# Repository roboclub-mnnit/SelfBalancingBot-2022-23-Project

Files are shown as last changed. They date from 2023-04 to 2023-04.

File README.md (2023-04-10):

# Self Balancing bot

## Robot Image



## Aim 

To balance a robot on two wheels at its normal position and control its movement through an Android app.

# Introduction

The aim of this project is to make an automated vehicle that balances itself without any outside help or support. This project is a rather complex one as it involves using PID Control and involuted programming. Self-balancing robots are unique among all others, just because of their ability to balance on a given fixed position. Even if the robot is displaced from its position, it is programmed so that it again recovers its position.

## Technology used

**On Robot:** Bluetooth, PID, TIMER Interrupt, Kalman Filter, Communication protocol (serial and I2C).

## Components

**MPU6050:** MPU6050 is a three-axis accelerometer and three-axis gyroscope Micro Electro-mechanical system (MEMS). It aids in the measurement of velocity, orientation, acceleration, displacement, and other motion-related features.

**Arduino Uno:** Arduino UNO is a low-cost, flexible, and easy-to-use programmable open-source microcontroller board that can be integrated into a variety of electronic projects. This board can be interfaced with other Arduino boards, Arduino shields, and Raspberry Pi boards and can control relays, LEDs, servos, and motors as an output.

**Drv8825 Motor driver:** The Drv8825 is a complete micro-stepping motor driver with a built-in translator for easy operation. It is designed to operate bipolar stepper motors in full-, half-, quarter-, eighth-, and sixteenth-step modes, with an output drive capacity of up to 45 V and ±2.2 A.

**Stepper Motor:** Stepper motors are a type of DC synchronous motor. Whereas the rotation of an induction motor is largely uncontrollable, the rotation of a stepper motor can be controlled with a remarkable degree of precision. Stepper motors can produce full, instantaneous torque - even from a standstill.

**ESP32:** ESP32 can perform as a complete standalone system or as a slave device to a host MCU, reducing communication stack overhead on the main application processor. ESP32 can interface with other systems to provide Wi-Fi and Bluetooth functionality through its SPI / SDIO or I2C / UART interfaces.

**Li-polymer battery:**  A lithium-polymer battery (LiPo) is a rechargeable battery that, in the case of true LiPo, uses solid polymer for the electrolyte and lithium for one of the electrodes. Commercially available LiPo is a hybrid: gel polymer or liquid electrolyte in a pouch format, more accurately termed a lithium-ion polymer battery.

**Jumper wire  :** Jumper wires typically come in three versions: male-to-male, male-to-female and female-to-female. The difference between each is in the endpoint of the wire. Male ends have a pin protruding and can plug into things, while female ends do not and are used to plug things into.

## Role of each software component-

**MPU6050 Data:** Initially MPU-6050 will measure the angle difference between the current position of the bot and its normal position. Now, this data is transferred to PID.

**PID Tuning:** PID will take input from MPU-6050 and accordingly calculate the PID value and give variable signals to both motors using interrupt service routine to bring the bot to its normal position and balance it.

**Bluetooth Communication:** Once the bot is balanced then we will send different commands ( forward, backward, turn left, turn right, and stop ) to the bot using Bluetooth communication to move the bot in different directions.

**ISR Command:** After receiving a command from Bluetooth, ISR will give different impulses to motors to move the bot according to the given command.

## Working of the bot

**1.** Turning the robot on.

**2.** The servo motor position is set to a minimum position to keep the robot in a standing position.

**3.** Receiving the data from Bluetooth.

**4.** Data is collected from the mpu-6050 and robot angle is calculated.

**5.** Data from MPU-6050 is filtered to remove the noise and make the data stable

**6.** Feeding the data in the PID controller and error is calculated by comparing it with the bot’s current angle and the balance point is delivered as output from the PID controller which will be in a linear data form.

**7.** Converting the linear PID balance point into a logarithmic balance point for running the stepper motor at variable speed.

**8.** Controlling the left and right motor separately.

**9.** **a** -->For controlling the left and right turn we changed the balance point of PID  for both motors separately.

**b** -->For moving forward and backward we have changed the target angle where the robot has to balance.
ex.--  Forward→increased target angle 
       Backward→decreased target angle

**10.** Starting the loop again from 3rd point.

## Features

- The robot balances on two wheels.
- We can move the robot left, right, forward, and backward.
- Option to set the PID constants from the onboard knob as well as wirelessly from the Android application.
- The robot stands on its own with a servo motor for calibration when powered on.
- We can reset the robot wirelessly in case it falls on the ground.
- Used PORT control of Arduino for making the pin high and low as it is 60 times faster than the digitalWrite function of Arduino. 

## Circuit diagram

Self balancing circuit

## App interface

bot

## App link

[Self balancing bot app.zip](https://github.com/sudhanshur555/SelfBalancingBot-2022-23-Project/files/11194098/Self.balancing.bot.app.zip)

## Source Code

[https://github.com/roboclub-mnnit/SelfBalancingBot-2022-23-Project](https://github.com/roboclub-mnnit/SelfBalancingBot-2022-23-Project)

## Video link

- https://youtu.be/lqwXdpySzbQ

## Real-life applications

- Self-balancing algorithms can be used in rocket propulsion systems.
- Can be used in warehouses for moving goods.
- It can be implemented on Segway.
- It can be used for surveillance in any terrain.

## Problem faced

**1.** MPU-6050 data has a lot of noise so we have a Kalman filter to smooth the data.

**2.** The setting of the PID value was frustrating when setting in code each time and checking the robot whether it is balanced or not. so we made three knobs to adjust the PID constant onboard without changing it in code and we also added this feature in the app so that the PID constant can also be set wirelessly.

**3.** Bluetooth connection gets lost regularly afterward we figured out that the input voltage was under 5v. So we powered the ESP32 directly with a battery with 11v.

**4.** When the potentiometer(for setting the PID constants) was powered with a 7805 voltage regulator(for 5v output) the robot oscillates as the servos were also connected to the 7805 and it drew a lot of power which made it undervolt(less than 5v)  and the value of constants gets changed when mapped in Arduino code. So we powered it directly with 5v of Arduino to get stable 5v.

**5.** Earlier we used TIMER1 interrupt (ISR) but later realized that it was causing the problem as servo library we have used also use TIMER1 to make PWM signal and delay function in Arduino uses TIMER0 for delay function so we have used the this Arduino ISR i.e TIMER2 for creating interrupt for making Stepper motor impulse.

**7.** Stepper motor was not turning at a very high speed so we have chosen an ISR of 200us as full speed for the stepper motor.

**8.** The bot was getting resettled in the setup part of the code in  which we had defined D13 as output and didn't work so we had defined the D13 as output in an “IF statement” in the loop part of the code.

**9.** To prevent the potentiometer and app PID constant from clashing with the original PID constant which we have set in code we have set a range so that we can deactivate the Potentiometer and app PID constant values when not needed and activate it only When the values Kp & Kd exceeds 10 and Ki exceeds 2.

**10.** Used PORT control of Arduino for making the pin high and low as it is 60 times faster than the digitalWrite function of Arduino and we have used it in ISR to make the impulse for driving the Stepper motor.

**11.** Detached the servo by software after running the main loop 200 times to prevent the oscillation of the servo and also prevent it further from drawing power from the battery.

**12.** Converted the linear output of PID value to nonlinear i.e in Logarithmic value to run the stepper motor at different speeds at different angles.

**13.** Controlled left and right Stepper motors separately for controlling the movement of the robot.

**14.** Made an Android app for controlling the movement of robots.

**15.** Separated the data coming from the app via Bluetooth in string form and stored it in different variables.

**16.** The PID error of Ki was getting very large and affected the responsiveness of the robot so we had limited it in range (-200 to 200).

**17.** There was a problem with the app that it was not showing any Bluetooth devices. Later we found that to connect it with Bluetooth it is first necessary to ask the app for accessing the phone’s Bluetooth. So we added the code in the app to ask for permission for accessing the Bluetooth from a user in the MIT app inventor. 

Note-This issue will only be faced in Android 9+ devices

**18.** Microstepping was used for smoother operation of the stepper motor.

**19.** Always disconnect the Rx and Tx pin of the Arduino while uploading the code to Arduino.

## Resources

 - Stepper motor control
   - Theory
     - https://youtu.be/09Mpkjcr0bo
     - https://youtu.be/eyqwLiowZiU
   - Programming
     - https://www.youtube.com/watch?v=7spK_BkMJys
 - Arduino
   - https://youtube.com/playlist?list=PLGs0VKk2DiYw-L-RibttcvK-WBZm8WLEP

- MPU6050
  - https://youtu.be/XCyRXMvVSCw
  - https://www.youtube.com/watch?v=7VW_XVbtu9k
  - https://youtu.be/yhz3bRQLvBY
  - https://youtu.be/Yh6mYF3VdFQ

- Battery
  - https://www.youtube.com/watch?v=Tye3dcBOqtY

- Servo motor
  - https://youtu.be/kUHmYKWwuWs

- HC-05 Bluetooth module
  - https://www.youtube.com/watch?v=yyjAAbxr0gM

- PID Controller
  - https://youtu.be/crw0Hcc67RY
  - https://youtu.be/t7ImNDOQIzM
  
- Communication 
  - https://youtu.be/IyGwvGzrqp8
  - https://youtu.be/fwGdmU2wi9s

- Filter
  - https://youtu.be/5HuN9iL-zxU

- Interrupt
  - https://youtu.be/Uv9UeYUsA8A

## Contributors

 - [Sudhanshu Ranjan](https://github.com/sudhanshur555)

 - [Abhishek Kumar Singh](https://github.com/Abhishekkumarsingh8957)

 - [Vikas]()

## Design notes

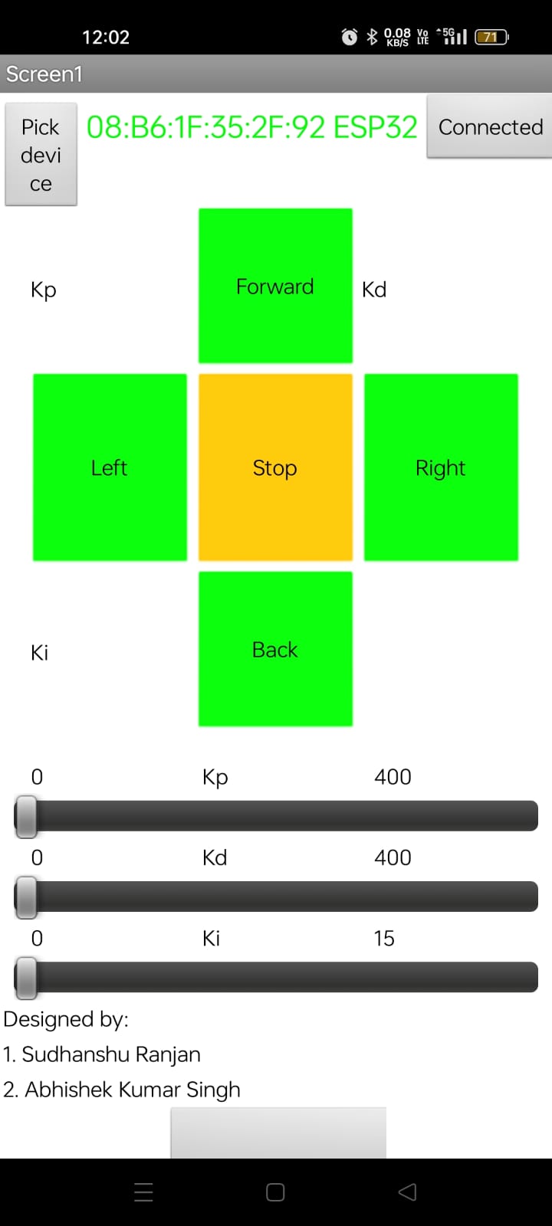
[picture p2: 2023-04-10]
App_interface.jpeg

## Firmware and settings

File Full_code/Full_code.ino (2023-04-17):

#include <Wire.h> //Included Wire library 

// bluetooth variable starts--------------------------------------------------


 int counter =0;
 char c;
 String dataIn;
 int8_t indexOfA,  indexOfB,  indexOfC,  indexOfD, indexOfE,  indexOfF,  indexOfG,  indexOfH ,indexOfI;

 String    data1,  data2,  data3,  data4, data5,  data6,  data7,  data8, data9;

 float newKp_bluetooth=0;
 float newKd_bluetooth=0;
 float newKi_bluetooth=0;

 bool F,B,L,R,S,startagain;

// bluetooth variable ends--------------------------------------------------


// potentiometer variable starts=============================================

float pot1=0;
float pot2=0;
float pot3=0;
float newkp_pot=0;
float newkd_pot=0;
float newki_pot=0;


// potentiometer variable ends=============================================


// servo declaration starts---------------------------------

  #include <Servo.h>
  Servo myservo1;  // create servo1 object to control a servo
  Servo myservo2;  // create servo2 object to control a servo
  unsigned long counter2=0;
// servo declaration ends---------------------------------

//mpu variable starts-------------------------------------

float RateRoll, RatePitch, RateYaw;
float RateCalibrationRoll, RateCalibrationPitch, RateCalibrationYaw;
float pitchTarget;
float pitch_Error;
int RateCalibrationNumber;
float AccX, AccY, AccZ;
float AngleRoll, AnglePitch;

//mpu variable ends--------------------------------------

//kalman filter variable starts--------------------------

float KalmanAngleRoll=0, KalmanUncertaintyAngleRoll=2*2;
float KalmanAnglePitch=0, KalmanUncertaintyAnglePitch=2*2;
float Kalman1DOutput[]={0,0};

//kalman filter variable ends--------------------------

//pid variable starts---------------------------------- 

float Kp=112;
float Kd=316;
float Ki=1.80;

float Kp_old=Kp;
float Kd_old=Kd;
float Ki_old=Ki;

//pid variable ends------------------------------------
float rotating_speed=100;

unsigned long milliOld;
unsigned long milliNew; 
unsigned long dt;


//Declaring global variables for mpu

float rollTarget=-4.70;
float rollActual;
float rollError=0;
float rollErrorOld;
float rollErrorChange;
float rollErrorSlope=0;
float rollErrorArea=0;
float rollBalance=0;
float rollBalance_left=0;
float rollBalance_right=0;


//Defining variable for motor
int New_speed_left;
int New_speed_right;
int speed_motor;
int ISR_counter_left=0;
int ISR_counter_right=0;
int Old_speed_left=0;
int Old_speed_right=0;


void setup() {
Serial.begin(57600);
// servo setup starts---------------------------------
   
   

   myservo1.attach(10);                 // attaches the servo on pin 10 to the servo object
   myservo2.attach(11);                 // attaches the servo on pin 11 to the servo object

   myservo1.write(5);                  // sets the servo position according to the scaled value
   delay(20);
   myservo2.write(20);                  // sets the servo position according to the scaled value
   delay(20);                           // waits for the servo to get there
   delay(2000);

// servo setup ends---------------------------------


  Wire.setClock(400000);  //Setting the clock frequency 400khz for I2C communication
  Wire.begin();
  delay(250);
  Wire.beginTransmission(0x68); 
  Wire.write(0x6B);
  Wire.write(0x00);
  Wire.endTransmission();


//Gyro calibration starts ----------------------------------------------------------------------------

 for (RateCalibrationNumber=0; RateCalibrationNumber<2000; RateCalibrationNumber ++) {  //rinning for loop 2000 times for calibration purpose
    gyro_signals();
    RateCalibrationRoll+=RateRoll;
    RateCalibrationPitch+=RatePitch;
    RateCalibrationYaw+=RateYaw;
    delay(1);
  }
  RateCalibrationRoll/=2000;
  RateCalibrationPitch/=2000;
  RateCalibrationYaw/=2000;  
//gyro calibration ends---------------------------------------------------------------------------------


angle();  //Called angle function


pinMode(A0, INPUT);             //Setting the A0 as input for using potentiometer as input for setting Kp
pinMode(A1, INPUT);             //Setting the A1 as input for using potentiometer as input for setting Kd
pinMode(A2, INPUT);             //Setting the A2 as input for using potentiometer as input for setting Ki

digitalWrite(5,HIGH);           // Setting direction pin of left stepper high for rotating it clockwise
digitalWrite(6,HIGH);           // Setting direction pin of right stepper high for rotating it clockwise
DDRD =B01101100;                //Setting PORTD of arduino to input and output from D2 to D7 by Direction register


//timer2 starts================================================================


   TCCR2A = 0;                                                               //Make sure that the TCCR2A register is set to zero
   TCCR2B = 0;                                                               //Make sure that the TCCR2A register is set to zero
   TIMSK2 |= (1 << OCIE2A);                                                  //Set the interupt enable bit OCIE2A in the TIMSK2 register
   TCCR2B |= (1 << CS21);                                                    //Set the CS21 bit in the TCCRB register to set the prescaler to 8
   TCCR2B |= (1 << CS20);                                                    //Set the CS21 bit in the TCCRB register to set the prescaler to 8
   OCR2A = 99;                                                               //The compare register is set to 200us
   TCCR2A |= (1 << WGM21);                                                   //Set counter 2 to CTC (clear timer on compare) mode


//timer2 ends==================================================================

  milliNew=micros();                                                         //stored current time in milli new for comparing it later

}

void loop() {
  
  //potentiometer  loop starts----------------------------------------------------
Serial.print("kp= ");
   Serial.print(Kp);
   Serial.print("kd= ");
   Serial.print(Kd);
   Serial.print("ki= ");
   Serial.print(Ki);
   Serial.print("rolltarget= ");
   Serial.println(rollTarget);
   
  pot1=analogRead(A0);            //Storing analog value of potentiometer at A0 in pot1 variable
  pot2=analogRead(A1);            //Storing analog value of potentiometer at A1 in pot2 variable
  pot3=analogRead(A2);            //Storing analog value of potentiometer at A2 in pot3 variable



  newkp_pot=map(pot1,0,1023,0,400);  //mapping the value of pot1 to 0-400 and storing it in variable newkp_pot
  newkd_pot=map(pot2,0,1023,0,400);  //mapping the value of pot2 to 0-400 and storing it in variable newkd_pot
  newki_pot=map(pot3,0,1023,0,1500); //mapping the value of pot3 to 0-1500 and storing it in variable newki_pot

  
  if(newkp_pot>10) Kp=newkp_pot;   //putting the condition that the value of newkp_pot will only stored in Kp when it is greater than 10
  if(newkd_pot>10) Kd=newkd_pot;   //putting the condition that the value of newkd_pot will only stored in Kd when it is greater than 10
  if(newki_pot>200) Ki=newki_pot/100;   //putting the condition that the value of newki_pot will only stored in Ki when it is greater than 200


  //potentiometer loop ends-----------------------------------



  //servo loop starts-----------------------------------

 counter2++;                           //increasing the counter2 by one when the servo code starts
 if(counter2>100)                      //executing the condition only when the main loop has already ran 100 times
 {
 myservo1.write(40);                  // sets the servo position to 40 degree
   
 myservo2.write(45);                  // sets the servo position 45 degree

 
 }

if(counter2>200)                      // it gets activated ehen counter2 get higher than 200 i.e the main loop ran 200 times
{

 myservo1.detach();                   //disconnect the servo1 and stop sending the signal to servo1
  myservo2.detach();                  //disconnect the servo1 and stop sending the signal to servo1
}

//servo loop ends----------------------------------------

//bluetooth loop begins=======================================================================



   while(Serial.available()>0)      //The loop activates when the serial buffer has data greater than 1 of arduino
   {
   c=Serial.read();                 //store the buffer data in string "c"
   if(c=='\n') {break;}             // when line change i.e "\n" is detected in string "c" then get out of while loop
   else        {dataIn+=c;}         
   }
   if(c=='\n')
   {
   Parse_the_Data();                //calling the function to storing the data in different variable from data1 to data 9

   F=data1.toInt();                 //Converting the string stored in data1 to integer and storing it in F for moving forward
   S=data2.toInt();                 //Converting the string stored in data2 to integer and storing it in S for stopping robot
   B=data3.toInt();                 //Converting the string stored in data3 to integer and storing it in B for moving robot backward
   
   R=data4.toInt();                 //Converting the string stored in data4 to integer and storing it in R  for turnibg robot rightward
   L=data5.toInt();                 //Converting the string stored in data5 to integer and storing it in L  for turning robot leftward
   newKp_bluetooth=data6.toFloat(); //Converting the string stored in data6 to integer and storing it in newKp_bluetooth  for setting Kp from app
   newKd_bluetooth=data7.toFloat(); //Converting the string stored in data7 to integer and storing it in newKd_bluetooth  for setting Kp from app
   newKi_bluetooth=data8.toFloat(); //Converting the string stored in data8 to integer and storing it in newKi_bluetooth  for setting Kp from app
   startagain=data9.toInt();        //Converting the string stored in data9 to integer and storing it in startagain for resetting arduino when reset button is pressed in app

   c=0;                             // deleting the data stored in "c" for storing new data from serial buffer memory of arduino
   dataIn="";                       // making dataIn blank
   }
  
   if(newKp_bluetooth>10) Kp=newKp_bluetooth;  //putting the condition that the value of newKp_bluetooth will only stored in Kp when it is greater than 10
   if(newKd_bluetooth>10) Kd=newKd_bluetooth;  //putting the condition that the value of newKd_bluetooth will only stored in Kd when it is greater than 10
   if(newKi_bluetooth>1.1) Ki=newKi_bluetooth;   //putting the condition that the value of newKi_bluetooth will only stored in Ki when it is greater than 2

//bluetooth loop ends==========================================================================




 angle();                          //Calling angle() function
  
 rollActual=KalmanAngleRoll;        //storing the current roll angle in rollActual
 
                                                 
 milliOld=milliNew;                 //storing the old time in milliNew
 milliNew=micros();                //storing the current time in milliNew for comparing it with milliold                                                                                              
 dt=milliNew-milliOld;             //Calculating the time difference bw milliNew and milliOld                                                                                         



  rollErrorOld=rollError;
  rollError=rollTarget-rollActual;                                                //error in roll angle wrt reference angle
  rollErrorChange=rollError-rollErrorOld;                                         //difference bw previous and current error
  rollErrorSlope=rollErrorChange/dt;                                              //Slope of error vs time
  rollErrorArea=rollErrorArea+rollError*dt;                                       //adding the previoud roll area and current area



  if(rollErrorArea > 200)rollErrorArea = 200;                                     //limiting the integral value for quicker response
  else if(rollErrorArea < -200)rollErrorArea = -200;

  rollBalance=Kp*rollError+Kd*rollErrorSlope+Ki*rollErrorArea;                    //Calculating the PID Balance point in rollBalance

   if(rollBalance < 10 && rollBalance > -10)rollBalance = 0;                      //consider the robot balanced when rollBalance is from -10to10 and setting rollBalance to 0.

  if(rollBalance > 400)rollBalance = 400;                                        //limit the PID-controller to the maximum controller output i.e 400
  else if(rollBalance < -400)rollBalance = -400;


  if(AngleRoll > 55 || AngleRoll < -55){                                           //stop the robot if it tilt greater than 55 degree
    rollBalance = 0;                                                             //Set the PID controller output to 0 so the motors stop moving
   } 

   
//for controlling bot via app------------------------------------------------------------------------------
 
rollBalance_left=rollBalance;                                                    // storing the value of rollBalance in rollBalance_left variable separately to control left motor separately.
rollBalance_right=rollBalance;                                                   // storing the value of rollBalance in rollBalance_right variable separately to control right motor separately.
 
 if(R==1 || L==1)                                                             //checking the command through bluetooth i.e. left or right
{
 counter++;
// Serial.print("  counter =" );
//  Serial.print(counter);
  if(R==1){                                                                   //rotating the bot in right direction
//     Serial.print("  Right Triggered " );
    rollBalance_left += rotating_speed;                                       //Increase the left motor speed
    rollBalance_right -= rotating_speed;                                      //Decrease the right motor speed
  }
  if(L==1){                                                                   //rotating the bot in left direction         
//    Serial.print("  Left Triggered " );       
    rollBalance_left -= rotating_speed;                                       //Decrease the left motor speed
    rollBalance_right += rotating_speed;                                      //Increase the right motor speed
  }

  
  
 if(counter>20)                                                               //turning the motor in left or right direction for 20 loops when left or right command is recieved through bluetooth
 {
  counter=0;
    R=0;
    L=0;
    F=0;
    B=0;
 }}
 if(F==1){                                                                   //checking for forward command through bluetooth
   rollTarget+=+0.3;                                                         //increasing the balance point of bot by 0.3 degree to move the bot in forward direction 
   F=0;                                                                      //setting again f=0 to avoid the continuous increment of 0.3 degree in set point in every loop
  }
 if(B==1){                                                                   //checking for backward command through bluetooth
    rollTarget+=-0.3;                                                        //decreasing the balance point of bot by 0.3 degree to move the bot in backward direction 
    B=0;                                                                     //setting again b=0 to avoid the continuous decrement of 0.3 degree in set point in every loop
    }   

 if(S==1){                                                                   //checking for stop command through bluetooth 
    rollTarget=-5.2;                                                         //setting the balance point of bot again to normal position i.e.-5.2 degree 
    R=0;                                                                     
    L=0;                                                                     //setting all other commands to zero to stop the bot and balance it at the current position
    F=0;
    B=0;
  }
  if(startagain==1){                  //resetting the arduino when reset buttomn is pressed in app and startagain becomes 1
 pinMode(12, OUTPUT);                //enable pin 12 as output
digitalWrite(12, HIGH);              // setting the D12 as high for resetting the arduino
  }
 
 
 
 
 
// for controlling bot via app-----------------------------------------------------------------------------------------------
 
 
 
 //Motor pulse calculations

//To compensate for the non-linear behaviour of the stepper motors the folowing calculations are needed to get a linear speed behaviour.
//for right motor---
if(rollBalance_right > 0)rollBalance_right = 404 - (1/(rollBalance_right + 9)) * 5500;           //changing the linar behaviour of rollbalance_right variable into logarithmic behaviour which is required to stepper motor
  else if(rollBalance_right < 0)rollBalance_right = -404 - (1/(rollBalance_right - 9)) * 5500;
  if(rollBalance_right > 0)New_speed_right = 394 - rollBalance_right;                            //Calculating the needed pulse time for the  stepper motor controllers
  else if(rollBalance_right < 0)New_speed_right = -394 - rollBalance_right;
  else New_speed_right = 0;


//for left motor----
  if(rollBalance_left > 0)rollBalance_left = 404 - (1/(rollBalance_left + 9)) * 5500;             //changing the linar behaviour of rollbalance_left variable into logarithmic behaviour which is required to stepper motor
  else if(rollBalance_left < 0)rollBalance_left = -404 - (1/(rollBalance_left - 9)) * 5500;
//Calculating the needed pulse time for the  stepper motor                                        //Calculating the needed pulse time for the  stepper motor controllers
  if(rollBalance_left > 0)New_speed_left = 394 - rollBalance_left;
  else if(rollBalance_left < 0)New_speed_left = -394 - rollBalance_left;
  else New_speed_left = 0;

}

//kalman filter function starts--------------------------------------------------------
//KalmanState is the predicted angle at each state , KalmanUncertainty is the uncertainty in predicted angle at each state 
//KalmanInput is the rotation rate is degree/secound measured by gyroscope , KalmanMeasurement is the angle measured by accelerometer trigonometry
void kalman_1d(float KalmanState, float KalmanUncertainty, float KalmanInput, float KalmanMeasurement) {                 
  KalmanState=KalmanState+0.004*KalmanInput;                                           //predicted angle(KalmanState) is calculated by adding previous predicted angle and angle change between previous state and current state             
  KalmanUncertainty=KalmanUncertainty + 0.004 * 0.004 * 4 * 4;                         //uncertainity in predicted angle(KalmanUncertainty) is calculated by adding uncertainity in previous state and iteration length
  float KalmanGain=KalmanUncertainty * 1/(1*KalmanUncertainty + 3 * 3);                //kalmangain is calulated here by ratio of predicted angle and accelerometer angle
  KalmanState=KalmanState+KalmanGain * (KalmanMeasurement-KalmanState);                //new predicted angle is calculated using kalmangain which is much accurate than previous one
  KalmanUncertainty=(1-KalmanGain) * KalmanUncertainty;                                //calculating uncertainity in new predicted angle using kalaman gain
  Kalman1DOutput[0]=KalmanState;                                                       //storing value of predicted angle(KalmanState) in Kalman1DOutput matrix at 0th index
  Kalman1DOutput[1]=KalmanUncertainty;                                                 //storing value of uncertainity in predicted angle(KalmanUncertainty) in Kalman1DOutput matrix at 1st index
}

//kalman filter function ends-----------------------------------------------------------

//gyro_signal function stats------------------------------------------------------------
//this fuction is used to calculate the angle using accelerometer trigonomentry
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

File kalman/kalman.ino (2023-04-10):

#include <Wire.h>
float RateRoll, RatePitch, RateYaw;
float RateCalibrationRoll, RateCalibrationPitch, RateCalibrationYaw;
float rollTarget,pitchTarget;
float Roll_Error,Pitch_Error;
int RateCalibrationNumber;
float AccX, AccY, AccZ;
float AngleRoll, AnglePitch;
uint32_t LoopTimer;
float KalmanAngleRoll=0, KalmanUncertaintyAngleRoll=2*2;
float KalmanAnglePitch=0, KalmanUncertaintyAnglePitch=2*2;
float Kalman1DOutput[]={0,0};
void kalman_1d(float KalmanState, float KalmanUncertainty, float KalmanInput, float KalmanMeasurement) {
  KalmanState=KalmanState+0.004*KalmanInput;
  KalmanUncertainty=KalmanUncertainty + 0.004 * 0.004 * 4 * 4;
  float KalmanGain=KalmanUncertainty * 1/(1*KalmanUncertainty + 3 * 3);
  KalmanState=KalmanState+KalmanGain * (KalmanMeasurement-KalmanState);
  KalmanUncertainty=(1-KalmanGain) * KalmanUncertainty;
  Kalman1DOutput[0]=KalmanState; 
  Kalman1DOutput[1]=KalmanUncertainty;
}
void gyro_signals(void) {
  Wire.beginTransmission(0x68);
  Wire.write(0x1A);
  Wire.write(0x05);
  Wire.endTransmission();
  Wire.beginTransmission(0x68);
  Wire.write(0x1C);
  Wire.write(0x10);
  Wire.endTransmission();
  Wire.beginTransmission(0x68);
  Wire.write(0x3B);
  Wire.endTransmission(); 
  Wire.requestFrom(0x68,6);
  int16_t AccXLSB = Wire.read() << 8 | Wire.read();
  int16_t AccYLSB = Wire.read() << 8 | Wire.read();
  int16_t AccZLSB = Wire.read() << 8 | Wire.read();
  Wire.beginTransmission(0x68);
  Wire.write(0x1B); 
  Wire.write(0x8);
  Wire.endTransmission();     
  Wire.beginTransmission(0x68);
  Wire.write(0x43);
  Wire.endTransmission();
  Wire.requestFrom(0x68,6);
  int16_t GyroX=Wire.read()<<8 | Wire.read();
  int16_t GyroY=Wire.read()<<8 | Wire.read();
  int16_t GyroZ=Wire.read()<<8 | Wire.read();
  RateRoll=(float)GyroX/65.5;
  RatePitch=(float)GyroY/65.5;
  RateYaw=(float)GyroZ/65.5;
  AccX=(float)AccXLSB/4096-0.01;
  AccY=(float)AccYLSB/4096-0.02;
  AccZ=(float)AccZLSB/4096+0.22;
  AngleRoll=atan(AccY/sqrt(AccX*AccX+AccZ*AccZ))*1/(3.142/180);
  AnglePitch=-atan(AccX/sqrt(AccY*AccY+AccZ*AccZ))*1/(3.142/180);
}
void setup() {
  Serial.begin(115200);
  pinMode(13, OUTPUT);
  digitalWrite(13, HIGH);
  Wire.setClock(400000);
  Wire.begin();
  delay(250);
  Wire.beginTransmission(0x68); 
  Wire.write(0x6B);
  Wire.write(0x00);
  Wire.endTransmission();
  for (RateCalibrationNumber=0; RateCalibrationNumber<2000; RateCalibrationNumber ++) {
    gyro_signals();
    RateCalibrationRoll+=RateRoll;
    RateCalibrationPitch+=RatePitch;
    RateCalibrationYaw+=RateYaw;
    delay(1);
  }
  RateCalibrationRoll/=2000;
  RateCalibrationPitch/=2000;
  RateCalibrationYaw/=2000;
  LoopTimer=micros();
  angle();
  rollTarget=KalmanAngleRoll;
  pitchTarget=KalmanAnglePitch;
}
void angle()
{
gyro_signals();
  RateRoll-=RateCalibrationRoll;
  RatePitch-=RateCalibrationPitch;
  RateYaw-=RateCalibrationYaw;
  kalman_1d(KalmanAngleRoll, KalmanUncertaintyAngleRoll, RateRoll, AngleRoll);
  KalmanAngleRoll=Kalman1DOutput[0]; 
  KalmanUncertaintyAngleRoll=Kalman1DOutput[1];
  kalman_1d(KalmanAnglePitch, KalmanUncertaintyAnglePitch, RatePitch, AnglePitch);
  KalmanAnglePitch=Kalman1DOutput[0]; 
  KalmanUncertaintyAnglePitch=Kalman1DOutput[1];
  Serial.print("Roll_Angle_[°] ");
  Serial.print(KalmanAngleRoll);
  Serial.print(" Pitch_Angle_[°] ");
  Serial.print(KalmanAnglePitch);
  while (micros() - LoopTimer < 4000);
  LoopTimer=micros();
}
void loop() {
  angle();
  Roll_Error=rollTarget-KalmanAngleRoll;
  Pitch_Error=pitchTarget-KalmanAnglePitch;
  Serial.print("Roll_Error_[°] ");
  Serial.print(Roll_Error);
  Serial.print(" Pitch_Error_[°] ");
  Serial.println(Pitch_Error);
}
